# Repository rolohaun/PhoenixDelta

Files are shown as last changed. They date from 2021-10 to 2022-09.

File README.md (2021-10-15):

# Phoenix Delta
DIY Delta Printer using Klipper firmware

This printer is a work in progress

Below are a list of parts I used to build it

- 3 x 1000mm 2020 Extrusion
- 9 x 400mm 2020 Extrusion
- 3 x Mellow 20T Idlers with teeth 3mm bore or 5mm bore depends on your corners
- 3 x Mellow 20T Pulley
- GT2 Timing Belt
- SKR Mini E3 2.0 Mainboard
- Raspberry Pi 3 B+
- Phaetus Dragon Hotend
- BMG Dual Gear Extruder
- Piezo bed level sensor
- 350mm Delta Print Bed
- 100 x M5 x 10mm Bolt
- 100 x M5 T-nut
- 100 x M5 T-nut Drop in type
- 3 x Optical Endstops

Where to Buy
MGN12H Rails
https://www.aliexpress.com/item/32806622073.html?spm=a2g0s.9042311.0.0.77354c4djpxj7L

Auto Level Probe
https://www.aliexpress.com/item/32841920169.html?spm=a2g0s.9042311.0.0.77354c4djpxj7L

Haydn Huntley Arms ( These can be bought from diffrent places )
https://www.magballarms.com/

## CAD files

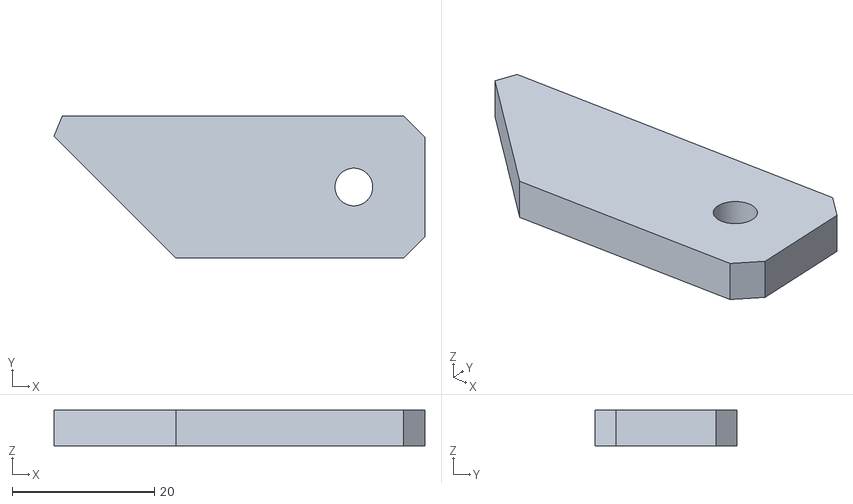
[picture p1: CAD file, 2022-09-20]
Bed_mount.stl
52.2 x 20.0 x 5.00

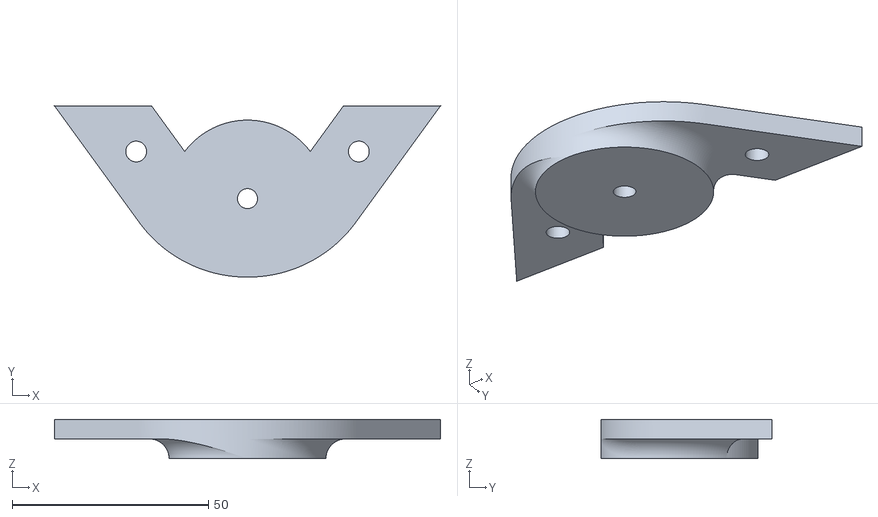
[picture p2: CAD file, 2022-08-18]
Phoenix_Foot.stl
98.4 x 43.6 x 10.0

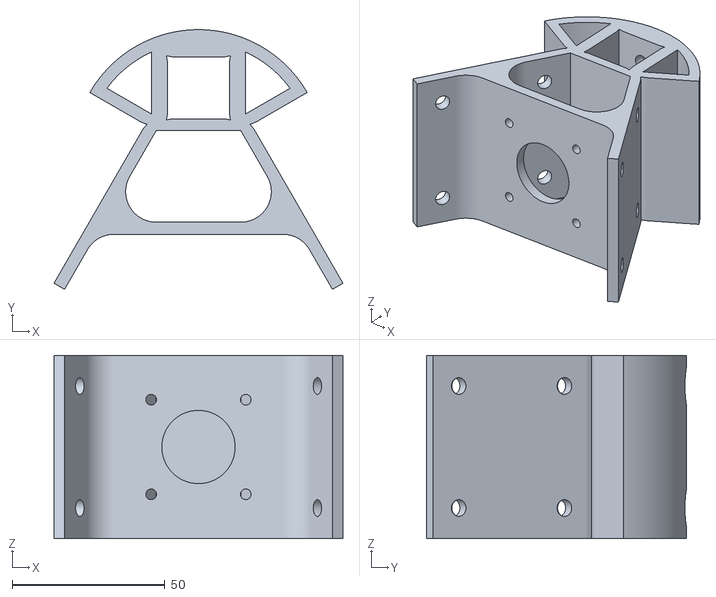
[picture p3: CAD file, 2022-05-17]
Phoenix_Motor_Mount_Frame.stl
94.7 x 85.1 x 60.0

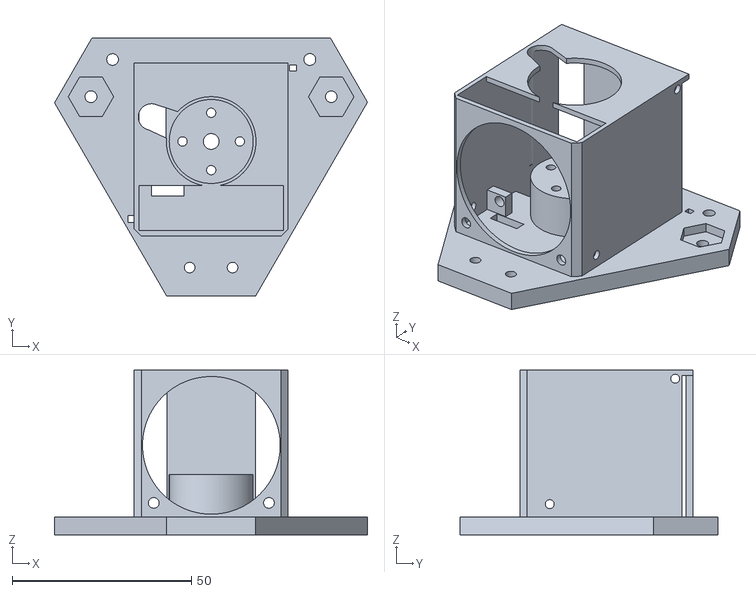
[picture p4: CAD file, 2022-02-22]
Effector_Bowden V2.stl
87.3 x 72.0 x 46.0

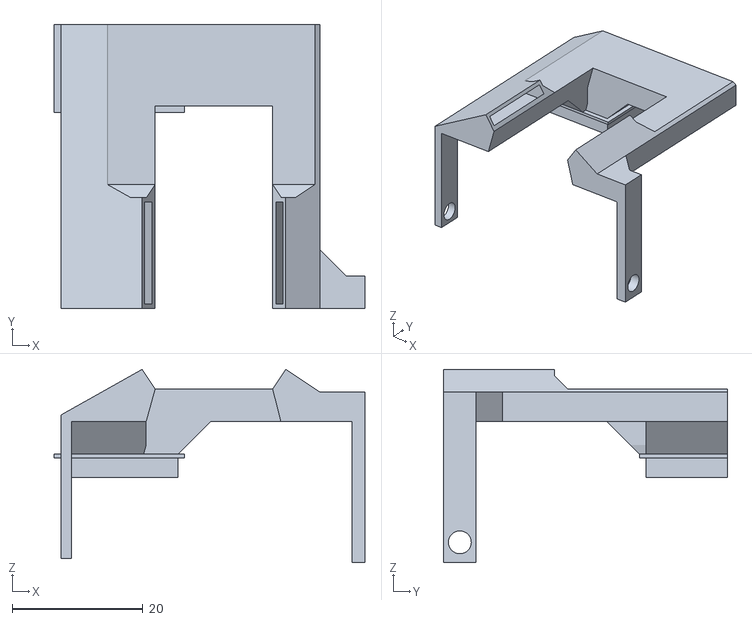
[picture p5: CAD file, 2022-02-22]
Part_Cooling_5015.stl
47.7 x 43.5 x 29.6

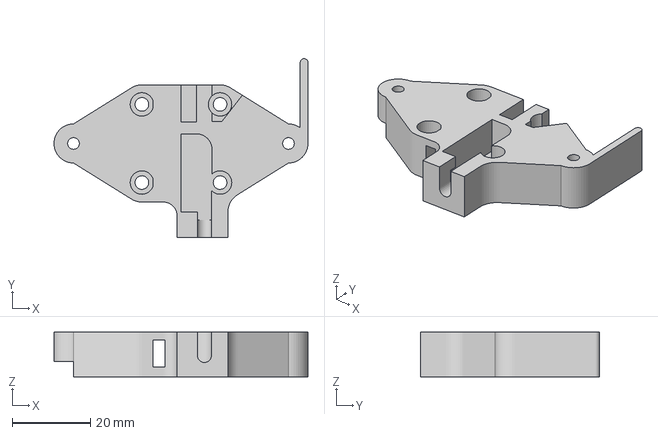
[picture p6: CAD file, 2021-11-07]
Phoenix Carriage.3mf
65.0 x 45.8 x 11.5 mm

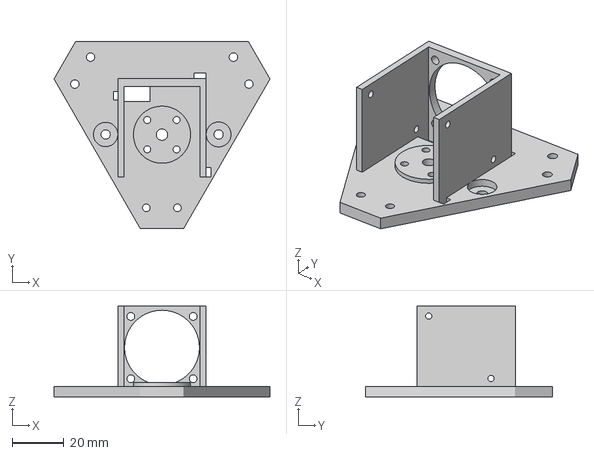
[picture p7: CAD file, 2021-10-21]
Effector_Direct_Sherpa.3mf
83.2 x 72.0 x 35.0 mm

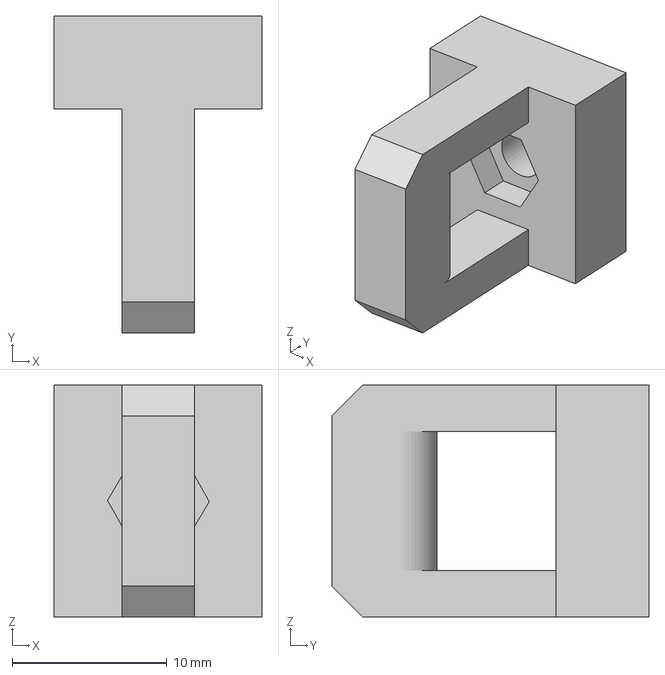
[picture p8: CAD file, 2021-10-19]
Phoenix Carriage Adjuster.3mf
13.5 x 20.5 x 15.0 mm

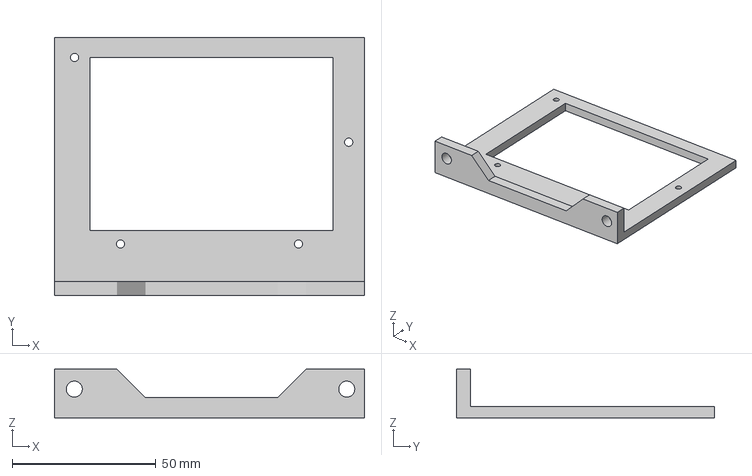
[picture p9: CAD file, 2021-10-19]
SKR_Mini_E3_Mount.3mf
108.0 x 90.0 x 16.9 mm

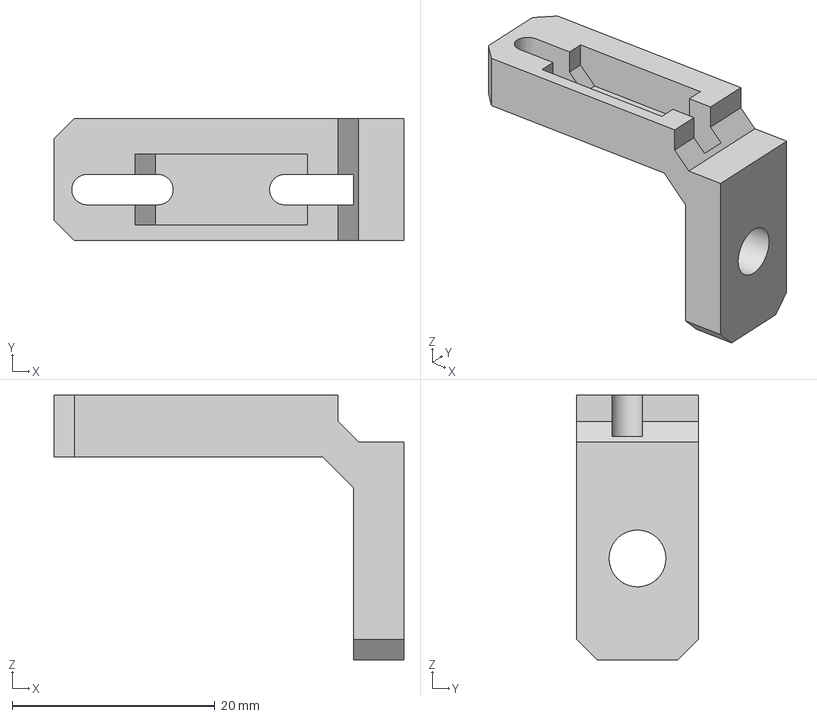
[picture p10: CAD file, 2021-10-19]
Endstop_Mount.3mf
34.5 x 12.0 x 26.1 mm

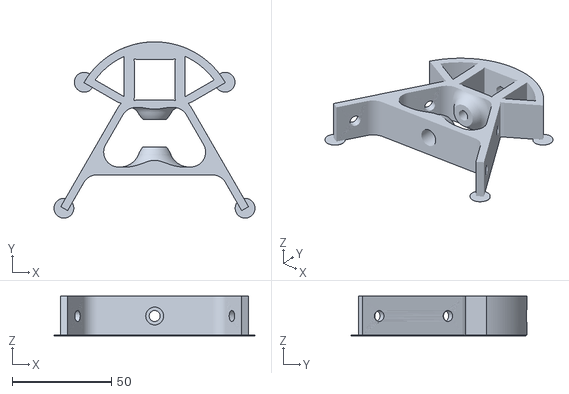
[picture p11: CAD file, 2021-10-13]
Phoenix_Top_Mount_Frame.stl
101.4 x 88.9 x 20.0

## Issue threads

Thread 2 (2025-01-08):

Piezo bed level sensor

abusaud64, 2025-01-08:
Hello rolohaun

Does Piezo bed level sensor work with you in klipper,
If yes will you please share .cfg file

rolohaun, 2025-01-10:
yes I use it on all my deltas it's just a normal endstop probe

[probe]
pin:!PA7
z_offset:0

abusaud64, 2025-01-10:
> yes I use it on all my deltas it's just a normal endstop probe
>
> [probe] pin:!PA7 z_offset:0

I thought you meant pin **PA1** in skr mini E3 V2 that dedicated for bltouch

But my question about sensor is the one that set under the heated bed like this picture
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

Or just you mean this one
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

As you test in your great helpful video https://youtu.be/lAmZb2f3-HI?feature=shared

rolohaun, 2025-01-10:
those don't work, use the one I recommend on here

https://www.aliexpress.com/item/32841920169.html?spm=a2g0s.9042311.0.0.77354c4djpxj7L

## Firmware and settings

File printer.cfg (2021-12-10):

[temperature_sensor mcu_temp]
sensor_type: temperature_mcu
min_temp: 0
max_temp: 100

[temperature_sensor raspberry_pi]
sensor_type: temperature_host
min_temp: 10
max_temp: 100


[virtual_sdcard]
path: ~/gcode_files

[display_status]

[pause_resume]

[gcode_macro PAUSE]
rename_existing: BASE_PAUSE
default_parameter_X: 230    #edit to your park position
default_parameter_Y: 230    #edit to your park position
default_parameter_Z: 10     #edit to your park position
default_parameter_E: 1      #edit to your retract length
gcode:
    SAVE_GCODE_STATE NAME=PAUSE_state
    BASE_PAUSE
    G91
    G1 E-{E} F2100
    G1 Z{Z}
    G90
    G1 X{X} Y{Y} F6000
    
[gcode_macro RESUME]
rename_existing: BASE_RESUME
default_parameter_E: 1      #edit to your retract length
gcode:
    G91
    G1 E{E} F2100
    G90
    RESTORE_GCODE_STATE NAME=PAUSE_state MOVE=1
    BASE_RESUME
    
[gcode_macro CANCEL_PRINT]
rename_existing: BASE_CANCEL_PRINT
gcode:
    TURN_OFF_HEATERS
    CLEAR_PAUSE
    SDCARD_RESET_FILE
    BASE_CANCEL_PRINT

[stepper_a]
step_pin: PB13
dir_pin: !PB12
enable_pin: !PB14
microsteps: 16
rotation_distance: 40
endstop_pin: ^PC0
position_endstop: 180 #required
homing_speed: 50
arm_length: 215 #required

[tmc2209 stepper_a]
uart_pin: PC11
tx_pin: PC10
uart_address: 0
run_current: 0.55
hold_current: 0.500
stealthchop_threshold: 999999

[stepper_b]
step_pin: PB10
dir_pin: !PB2
enable_pin: !PB11
microsteps: 16
rotation_distance: 40
endstop_pin: ^PC1

[tmc2209 stepper_b]
uart_pin: PC11
tx_pin: PC10
uart_address: 2
run_current: 0.55
hold_current: 0.500
stealthchop_threshold: 999999

[stepper_c]
step_pin: PB0
dir_pin: !PC5
enable_pin: !PB1
microsteps: 16
rotation_distance: 40
endstop_pin: ^PC2

[tmc2209 stepper_c]
uart_pin: PC11
tx_pin: PC10
uart_address: 1
run_current: 0.55
hold_current: 0.500
stealthchop_threshold: 999999

[extruder]
step_pin: PB3
dir_pin: PB4
enable_pin: !PD2
microsteps: 16
rotation_distance: 7.696
nozzle_diameter: 0.400
filament_diameter: 1.750
heater_pin: PC8
sensor_type: EPCOS 100K B57560G104F
sensor_pin: PC3
control: pid
pid_Kp: 21.527
pid_Ki: 1.063
pid_Kd: 108.982
min_temp: 0
min_extrude_temp: 0
max_temp: 300
#pressure_advance = 0.708

[tmc2209 extruder]
uart_pin: PC11
tx_pin: PC10
uart_address: 3
run_current: 0.45
hold_current: 0.45
#stealthchop_threshold: 5

[endstop_phase]

[heater_fan nozzle_cooling_fan]
pin: PC7

[fan]
pin: PC6

[mcu]
serial: /dev/serial/by-id/usb-Klipper_Klipper_firmware_12345-if00


[resonance_tester]
accel_chip: adxl345
probe_points:
    -0.26,1.20,22.14  # an example

[printer]
kinematics: delta
max_velocity: 300
max_accel: 3000
max_z_velocity: 150
minimum_z_position=-5
delta_radius: 90 #required

[probe]
pin: !PA1
speed: 45
z_offset: 0

[delta_calibrate]
radius: 150
horizontal_move_z: 25
Speed: 50

[static_digital_output usb_pullup_enable]
pins: !PA14

[board_pins]
aliases:
    # EXP1 header
    EXP1_1=PB5, EXP1_3=PA9,   EXP1_5=PA10, EXP1_7=PB8, EXP1_9=<GND>,
    EXP1_2=PA15, EXP1_4=<RST>, EXP1_6=PB9,  EXP1_8=PB15, EXP1_10=<5V>

# See the sample-lcd.cfg file for definitions of common LCD displays.
